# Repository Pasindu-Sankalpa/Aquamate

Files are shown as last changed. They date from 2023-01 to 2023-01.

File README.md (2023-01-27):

<b><h2><center>Problem Description</center></h1></b>

Although it is unpopular, fish breeding is an important source of foreign exchange for Sri Lanka. In the middle level it is self-employment for a vast population. Not only that, most of the people also have a home aquarium to refresh their minds. Accordingly, we can conclude that fish breeding has been spread to each level in society.

Temperature of water, pH level and turbidity are the main parameters which the fish breeders should keep on track regarding the safety of their farm. But as we observed, there is no such system deployed to measure these parameters in real time even in mass scale aquariums in Sri Lanka. Hence, this can lead to economic disasters if a parameter change happens. Another problem we can identify is the need of employees for feeding. Commonly, feeding is done once or twice per day. Therefore, if we can automate this process, it would be beneficial for the farm owners.

Our solution is Aquamate. A monitoring and automatic feeding system for mass scale aquariums in Sri Lanka.

Please refer the documents for more information

Visit <http://aquamate-global.web.app/>

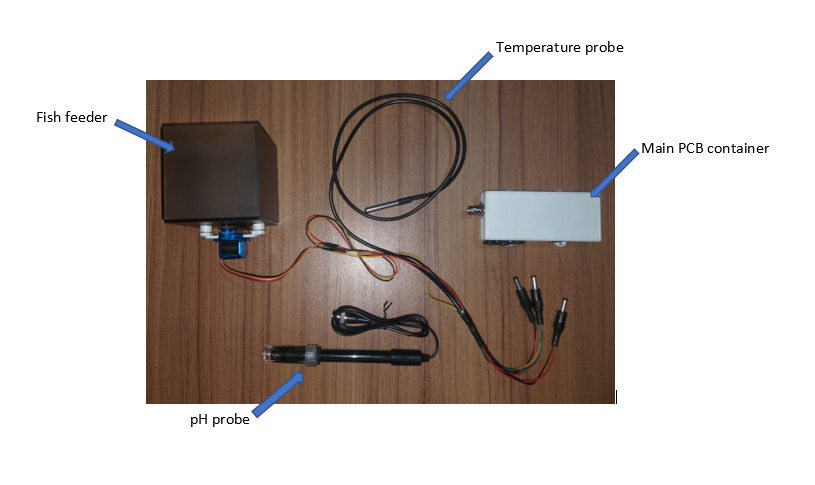
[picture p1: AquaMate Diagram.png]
AquaMate indoor unit

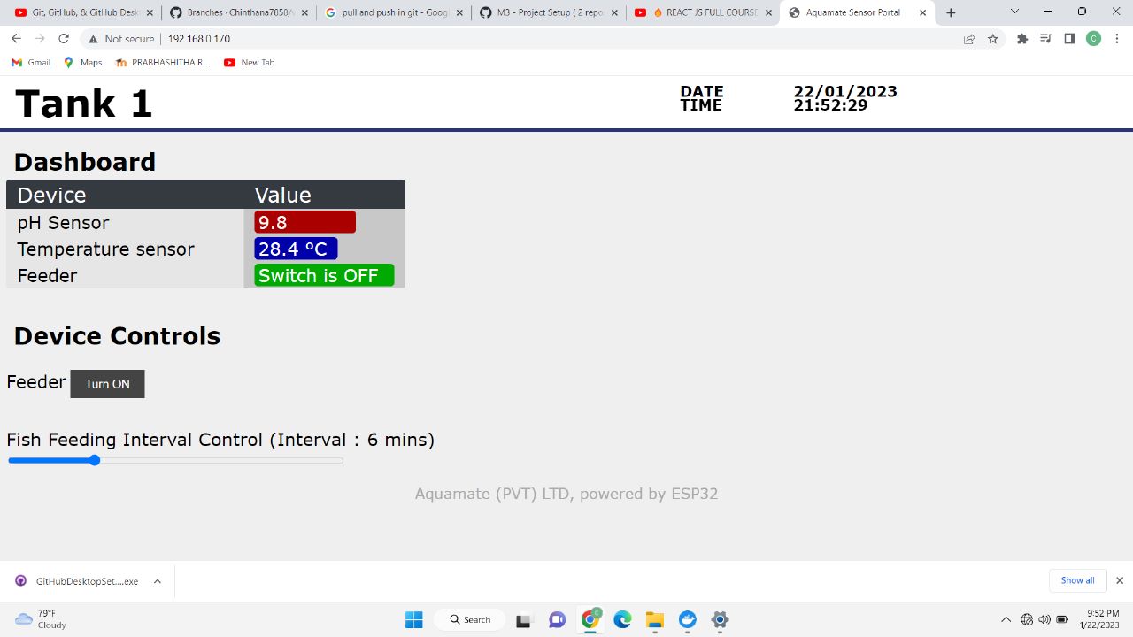
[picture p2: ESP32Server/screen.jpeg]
AquaMate server


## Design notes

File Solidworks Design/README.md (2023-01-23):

<b><h2><center>Enclosure Design</center></h1></b>

Enclosure design was designed with SOLIDWORKS 2020. There are two main parts such that fish feeder and main PCB container.

<br>
<br>

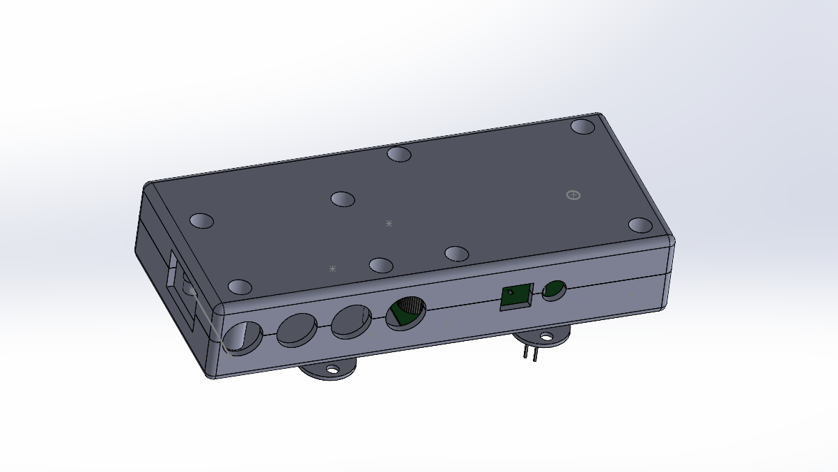
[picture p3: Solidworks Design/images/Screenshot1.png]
header image

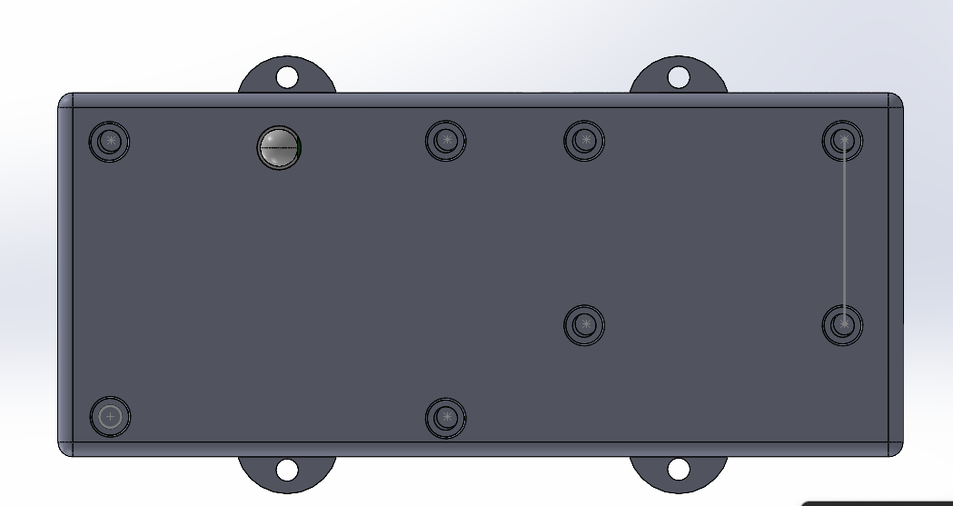
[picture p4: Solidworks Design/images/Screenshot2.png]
header image

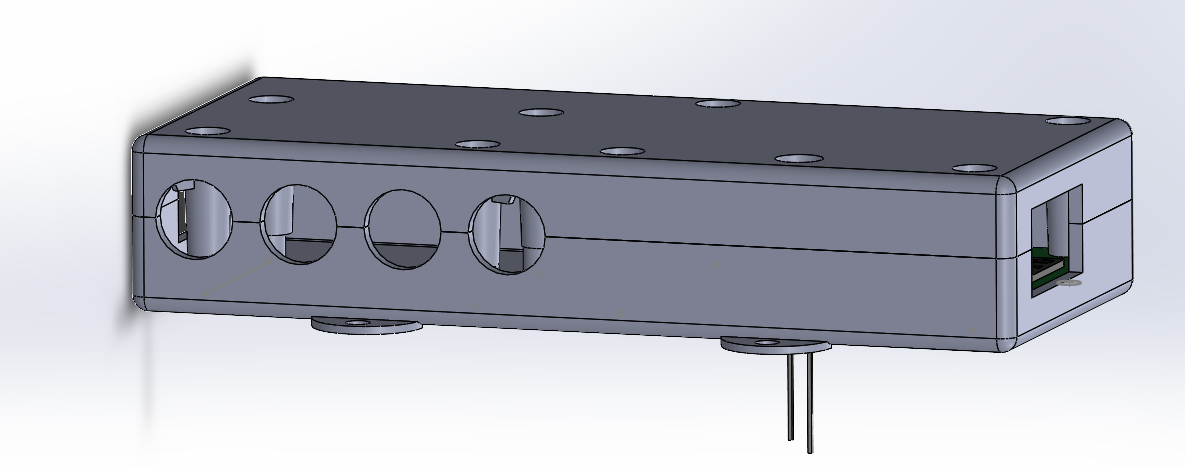
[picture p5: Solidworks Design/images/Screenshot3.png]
header image

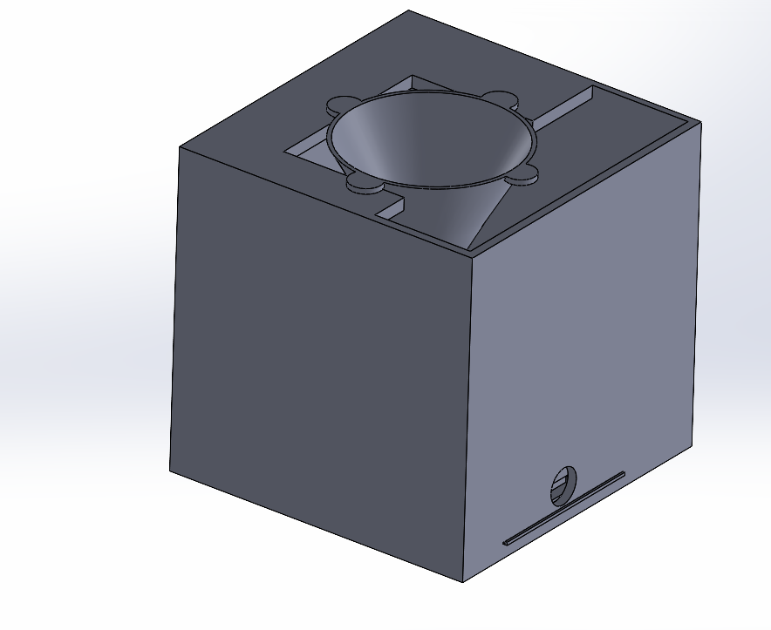
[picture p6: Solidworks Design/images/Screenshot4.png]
header image


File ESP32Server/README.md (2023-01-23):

<b><h2><center>Sampe code for updating a web page and getting user actions sent back the the microcontroller</center></h1></b>

This sample code will show you how to create an access point, serve a web page, updated just changed data, and get user interactions such as button presses and slider actions sent back to the microcontrller.

You will need an ESP32 and some open source libraries.

<br>
<br>

header image

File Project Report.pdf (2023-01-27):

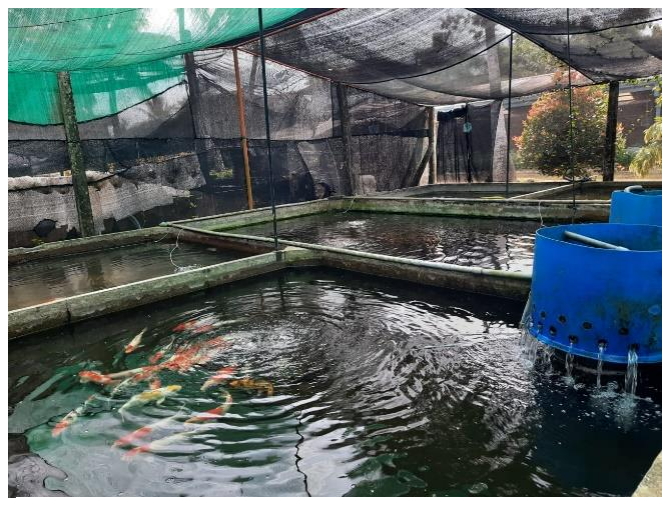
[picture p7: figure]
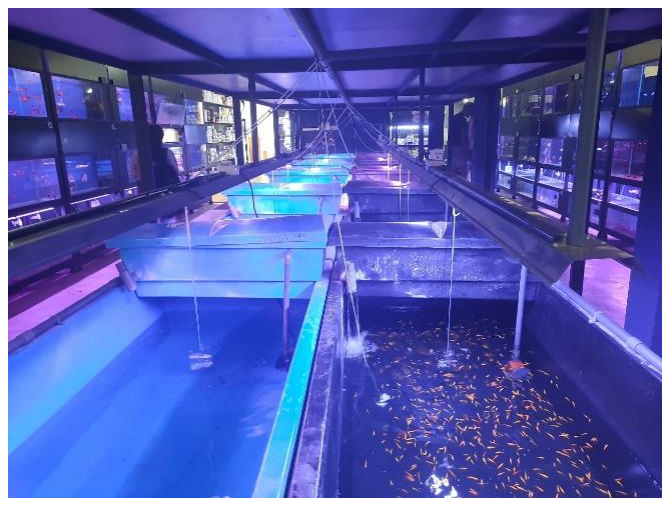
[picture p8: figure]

Figure: Indoor tank | Figure: Outdoor tank

## 1. Problem Description

Although it is unpopular, fish breeding is an important source of foreign exchange for Sri Lanka. In the middle level it is self-employment for a vast population. Not only that, most of the people also have a home aquarium to refresh their minds. Accordingly, we can conclude that fish breeding has been spread to each level in society.

Temperature of water, pH level and turbidity are the main parameters which the fish breeders should keep on track regarding the safety of their farm. But as we observed, there is no such system deployed to measure these parameters in real time even in mass scale aquariums in Sri Lanka. Hence, this can lead to economic disasters if a parameter change happens. Another problem we can identify is the need of employees for feeding. Commonly, feeding is done once or twice per day. Therefore, if we can automate this process, it would be beneficial for the farm owners.

Several aquarium monitoring systems are available in the global market. The problems we can identify, when we are going to deploy them in Sri Lanka are,
1. High cost (approximately $ 500 per unit for an industrial level equipment)
2. Requirement of periodic service (this is also problematic because no service center located in Sri Lanka)

## 2. Problem Validation

We visited Angel Aquarium (pvt) Ltd. which is one of mass scale aquarium in Sri Lanka to get a better understanding regarding the problem. As explained in the above section they are also hoping to deploy this kind of system but the initial cost to purchase them from the global market is not affordable for them. This was a huge motivation for our team.

By this discussion, we could gather important information regarding the precious water parameters for fishes and feeding patterns. Another important fact we observed is that the pH level is critical for indoor fish species while the turbidity is the important parameter for the outdoor species. pH level is not critical for outdoor species since they have been adopted for varies pH levels such as rainy water, but the high turbidity can damage their branchia. However, temperature is critical for both indoor and outdoor species.

## 3. Solution

Our solution is Aquamate. A monitoring and automation system for mass scale aquariums in Sri Lanka. Our mission is to provide this product in an affordable price.

Under the reasons explained earlier, we introduce two separate units for indoor and outdoor tanks. By this method we can reduce the cost for un-necessary sensors.

Under this project we implement only the indoor unit. Table 1 lists the features each unit has. The feeder is programmable via the dashboard to feed at any time interval.

Feature | Indoor Unit | Outdoor Unit
Temperature sensor | Yes | Yes
pH sensor | Yes | No
Turbidity sensor | No | Yes
Feeder | Yes | Yes
Dashboard | Yes | Yes

## 4. Implementation

### 4.1 Component Selection

Follows are how we selected the critical components of our device.

Micro controller: Selected micro controller is ESP32 wroom 32 (https://www.espressif.com/sites/default/files/documentation/esp32-wroom-32_datasheet_en.pdf) considering its WiFi capability and low power usage. ESP8266 is also a good alternative which comes under the same family with low price, however since we need two ADC lines we had to move to ESP32 wroom 32 with the an additional cost.

pH sensor: Gravity: Analog pH Sensor (https://www.dfrobot.com/product-2069.html) which comes with an industrial level probe is selected considering its considerable accuracy and relative low cost.

Temperature sensor: DS18B20 (https://www.analog.com/media/en/technical-documentation/data-sheets/ds18b20.pdf) is selected. It is water resist and has an excellent accuracy.

### 4.2 Circuit Design and Initial Testing

The device is planned to be powered by a 9V supply. There are two reasons behind this decision

1. If we use 230V AC current to power the device, there has to be a 230V AC current wiring around the aquarium. Since aquariums always deal with water, we decided to power the device with 9V considering the user safety in a case of current leakage.
2. Additionally, it reduces the cost per unit since multiple devices can be powered with a single power supply. No need of adding a transformer and relative circuitry for every device.

Table 1: Features of units

There are two voltage regulator ICs inside a device. AMS1117-3.3v regulator is used to power the micro controller and the temperature sensor. AMS1117-5v regulator is used to power the pH sensor and feeder.

Initial testing was carried out using a ESP32 development kit. A breadboard prototype was implemented to test the sensors. Temperature sensor was tested in our own and pH sensor was tested with the help of department of material science and engineering.

### 4.3 Printed Circuit Board Design

Printed circuit board was designed with Altium Designer 21.0.8. It was two-layer design. Two push buttons were added on the PCB for testing purposes and can be removed in a mass scale manufacturing.

Manufacturing was done at JLCPCB in China. Therefore, online available JLCPCB design rules were imported to Altium Designer.

Refer Appendix A and Appendix B for schematic diagram and layout respectively.

### 4.4 Enclosure Design

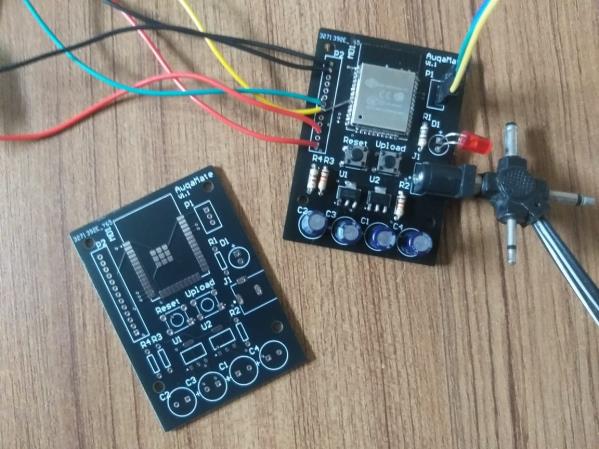
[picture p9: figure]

Enclosure design was designed with SOLIDWORKS 2020. There are two main parts such that fish feeder and main PCB container.

### 4.4.1 Fish feeder

This is a cube shaped box. There is a lid that opens and closes to fall fish seeds into the tank at the specified time interval. There are two mounting bosses in the bottom side to fix the servo motor that is used to open and close the lid.

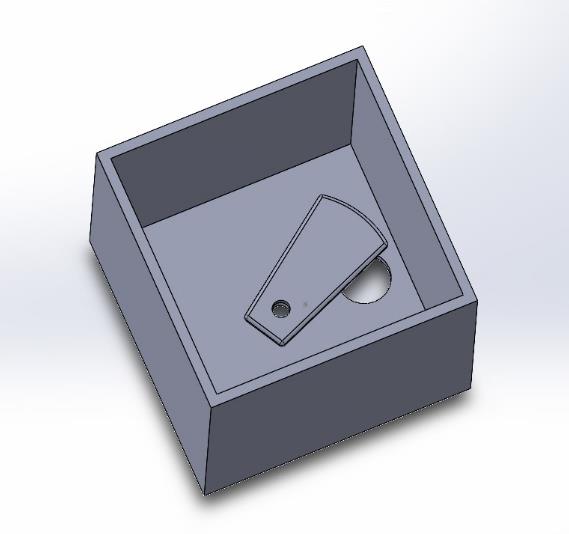
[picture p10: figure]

### 4.4.2 Main PCB Container

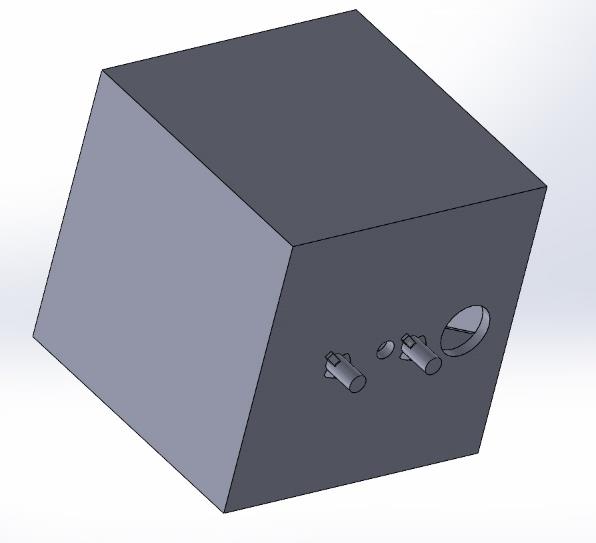
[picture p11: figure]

This was designed to contain the main PCB and pH sensor unit. Two circuit parts are fixed to the box using four mounting bosses. There are four holes to fix sensors.

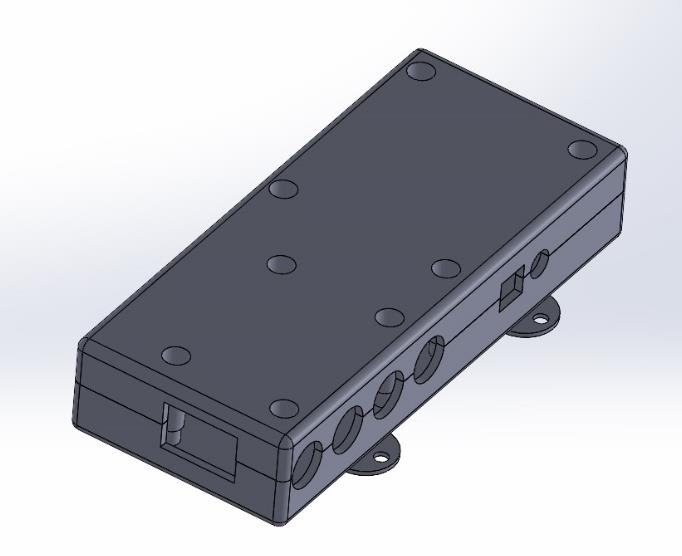
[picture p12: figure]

### 4.5 Web Development

### 4.5.1 Web Page

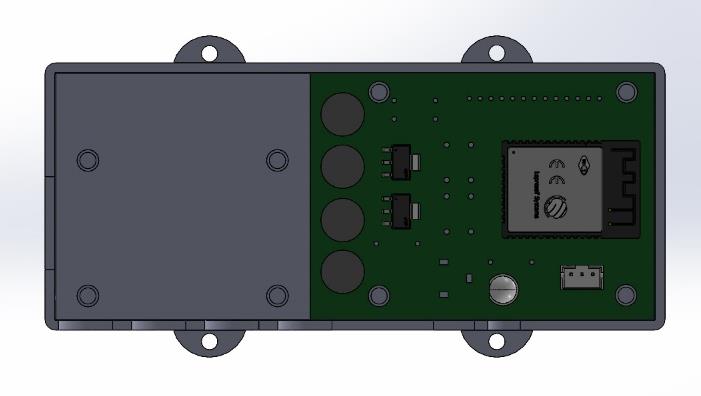
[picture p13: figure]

Main web site can be accessed by anyone using the link http://aquamate-global.web.app. An image of interface is shown below.

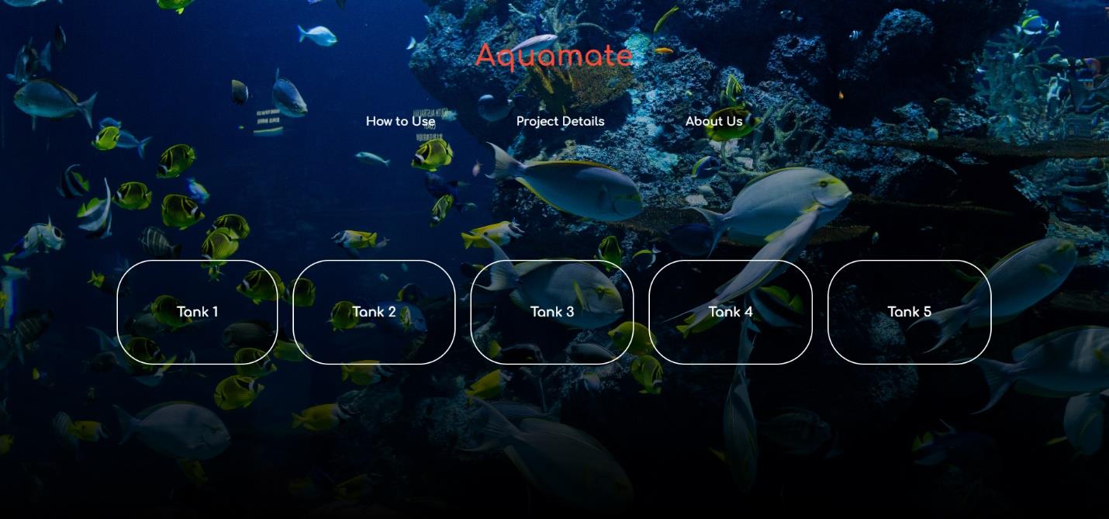
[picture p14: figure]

Users can click relevant button with tank name to see the corresponding dashboard. It will pop-up in a new window. But those details can only be accessed by the people who have connected to the same local network, as same network which the Aquamate device is connected.

If the user is powering up the Aquamate device for the very first time, there is a small configuration needs to be done. Those details are shown in the web page as well.

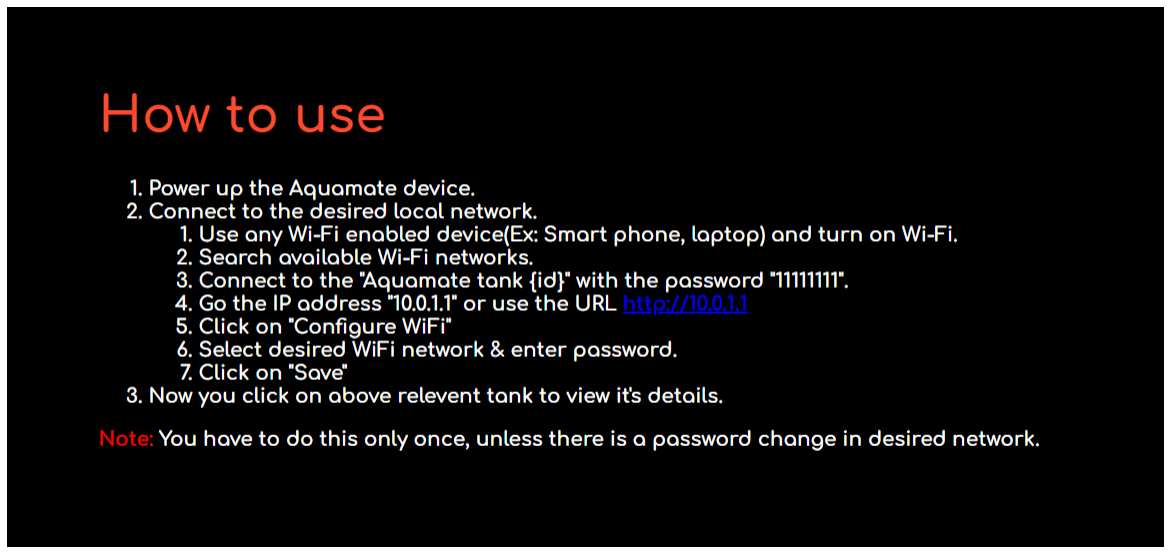
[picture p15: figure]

Above steps can be carried out by anyone who has basic knowledge of computer networks. Most importantly, these steps need to be done only once for each device. After that when powering on, Aquamate device will automatically connect to the previously configured local network.

### 4.5.2 ESP32 Web Server

Each Aquamate device has a web server running inside the ESP32 micro controller. After connected to the local network, it will send real time data of pH value, temperature, feeder on/off status to the web site continuously. So, the users can view the data.

pH progress bar shows pH values from 0 to 14 as standard scale. And temperature progress bar shows temperature values from 0ºC to 50ºC. If pH value or temperature value is too low or too high, color of the progress bar will change from blue to red. An instance of dashboard of a tank is shown below.

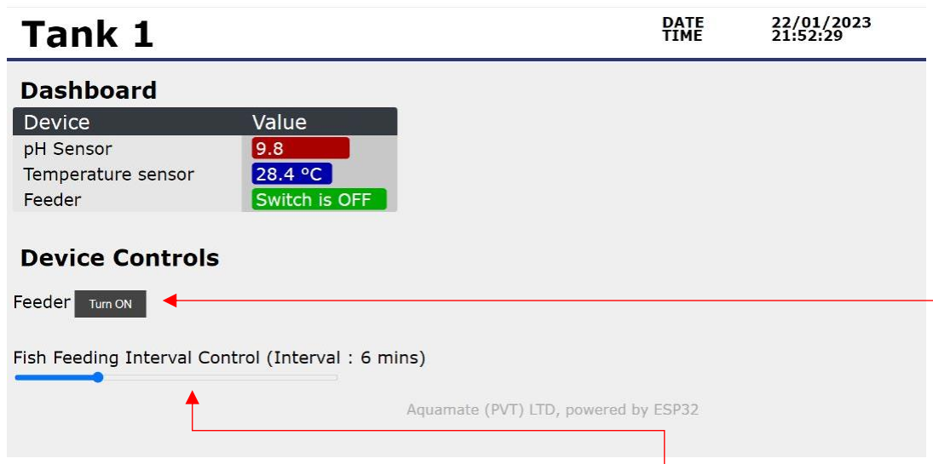
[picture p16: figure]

As well as users can set the fish feeding time interval using the slider in web page and feeder on/off switch. Slider can change the fish feeding interval between 1 to 24 hours. Those data will send back to the ESP32 web server and will act accordingly.

### 4.6 Final Testing

After completing and assembling all components a final testing was carried out to check the overall functionality. Things works perfectly and communicate with the web server without any failure. Figure below shows the parts of Aquamate indoor unit.

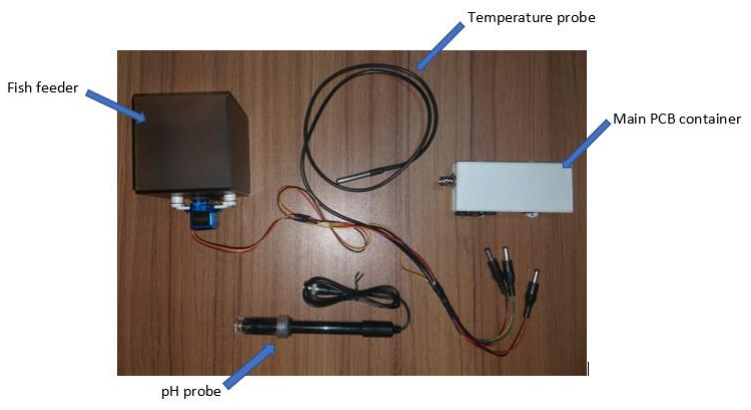
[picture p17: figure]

## Appendix A

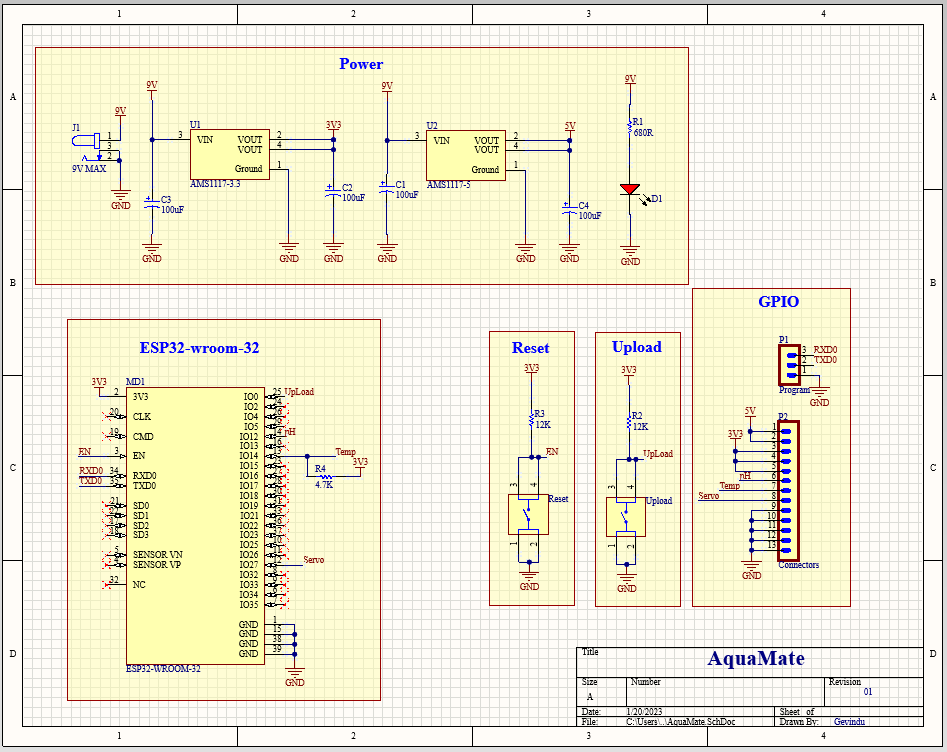
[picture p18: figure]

## Appendix B

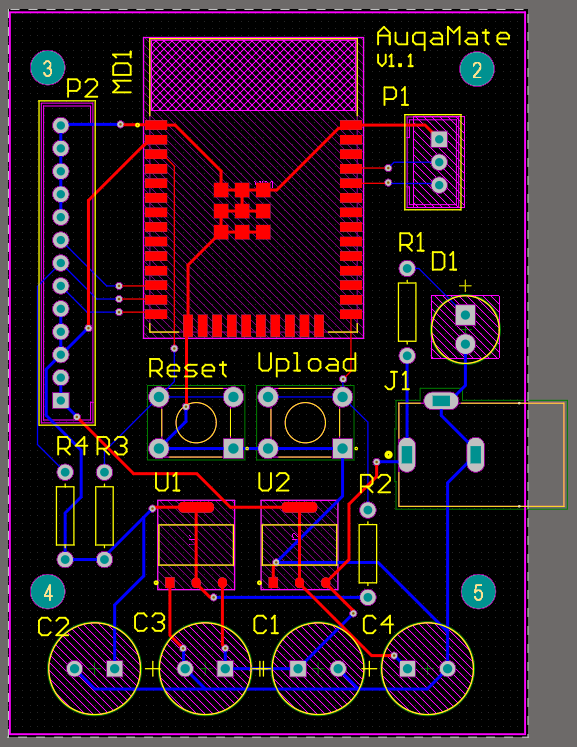
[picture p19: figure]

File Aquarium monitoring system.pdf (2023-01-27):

# Aquamate

Aquamate is an aquarium monitoring and automation system for mass scale aquariums in Sri Lanka. we introduce two separate units for indoor and outdoor tanks. By this method we can reduce the cost for un-necessary sensors. We implement only the indoor unit. We used temperature sensor and pH sensor for this unit. We can measure pH value and temperature of indoor tank. There is a dashboard for this unit. Parallelly, we designed a fish feeder. The fish feeder is programmable via the dashboard to feed at any time interval.

Mainly there are two main parts of this unit. They are fish feeder and PCB contained box. pH sensor unit and main PCB is contained in this box. All sensors are connected to this box. Fish feeder is a cube shaped box. There is a lid that opens and closes to fall fish seeds into the tank at the specified time interval.

This is a user-friendly monitoring system. We have a web page and user can watch necessary information of the fish tank through that webpage. And also, user can control the fish feeder unit through this webpage. You can connect several tanks to monitoring system. Each tank has separate tab in our webpage. Our sensors are smoothly calibrated and you will have more accurate values. Our main unit is waterproof and well designed.

Main web site can be accessed by anyone using the link http://aquamate-global.web.app. Users can click relevant button with tank name to see the corresponding dashboard. It will pop-up in a new window. But those details can only be accessed by the people who have connected to the same local network, as same network which the Aquamate device is connected. If the user is powering up the Aquamate device for the very first time, there is a small configuration needs to be done. Those details are shown in the web page as well. Those steps can be carried out by anyone who has basic knowledge of computer networks. Most importantly, these steps need to be done only once for each device. After that when powering on, Aquamate device will automatically connect to the previously configured local network.

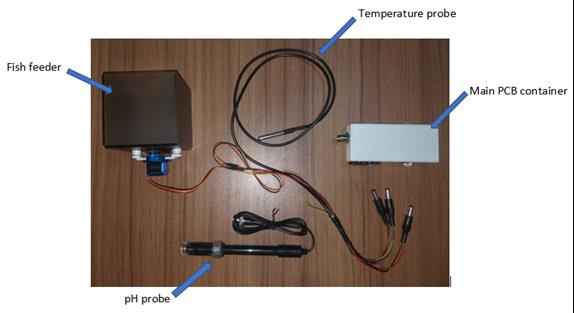
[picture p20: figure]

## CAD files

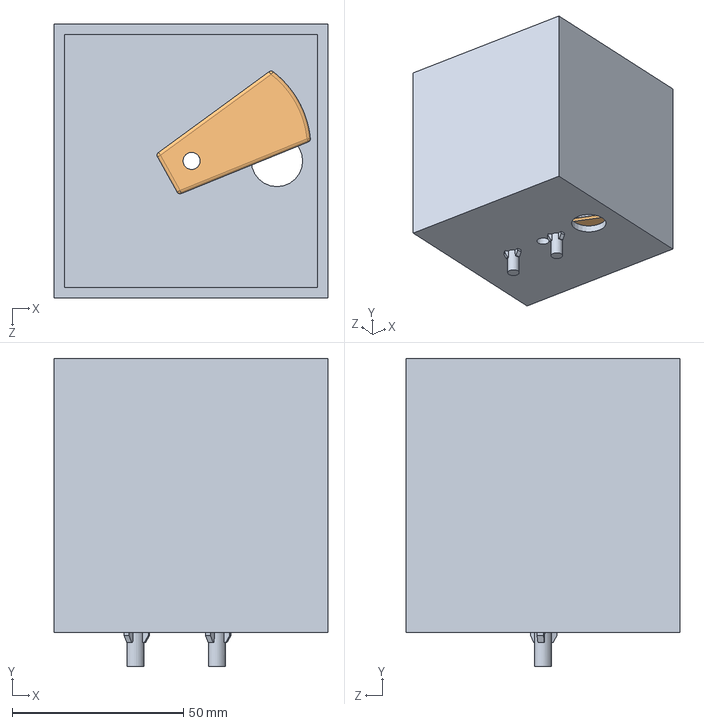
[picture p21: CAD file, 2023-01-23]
Solidworks Design/Fish_feeder.SLDASM
80.0 x 90.0 x 80.0 mm
Part1^Assem2
Part2^Assem2

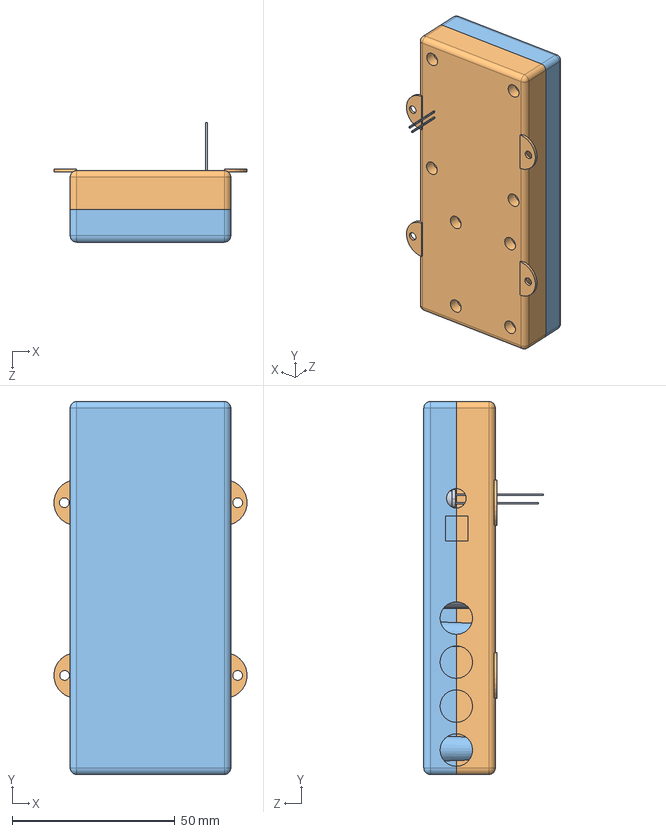
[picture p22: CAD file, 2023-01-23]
Solidworks Design/Main_pcb.SLDASM
59.2 x 114.5 x 36.7 mm
AquaMate.step
Part2^Assem1
Part3^Assem1

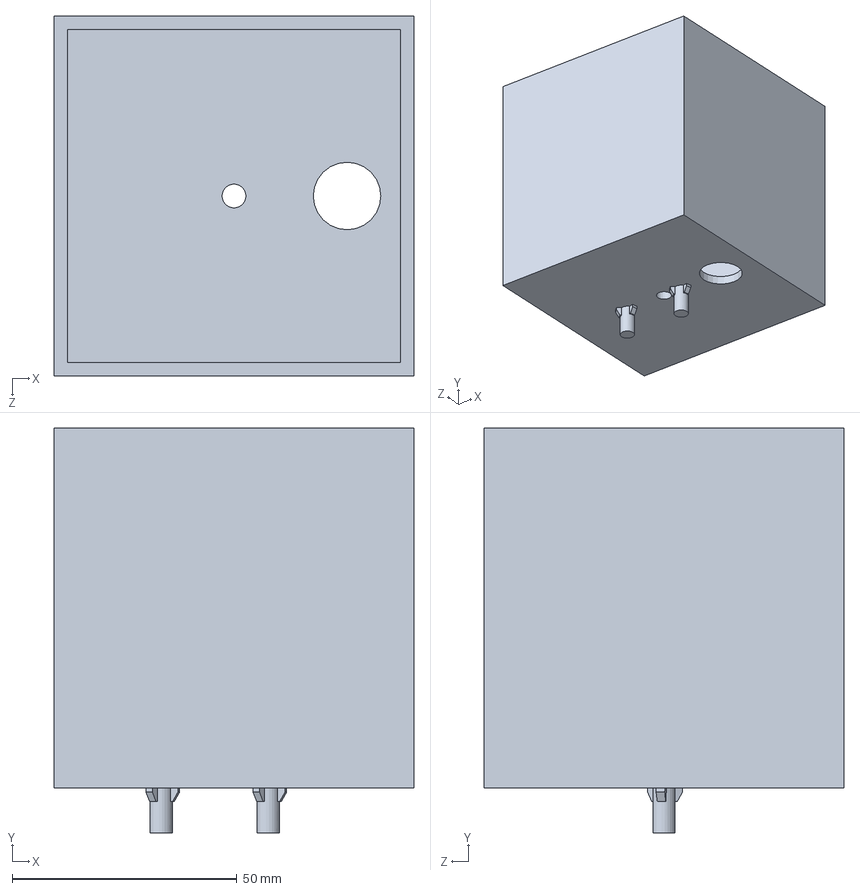
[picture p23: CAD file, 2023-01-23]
Solidworks Design/Part1^Assem2.SLDPRT
80.0 x 90.0 x 80.0 mm

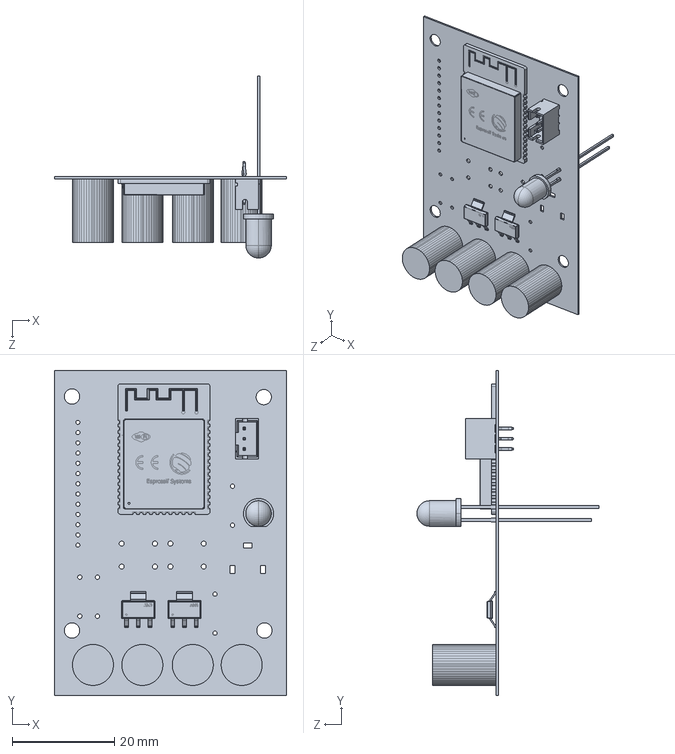
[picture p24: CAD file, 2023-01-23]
Solidworks Design/AquaMate.step.SLDPRT
45.3 x 63.5 x 35.6 mm

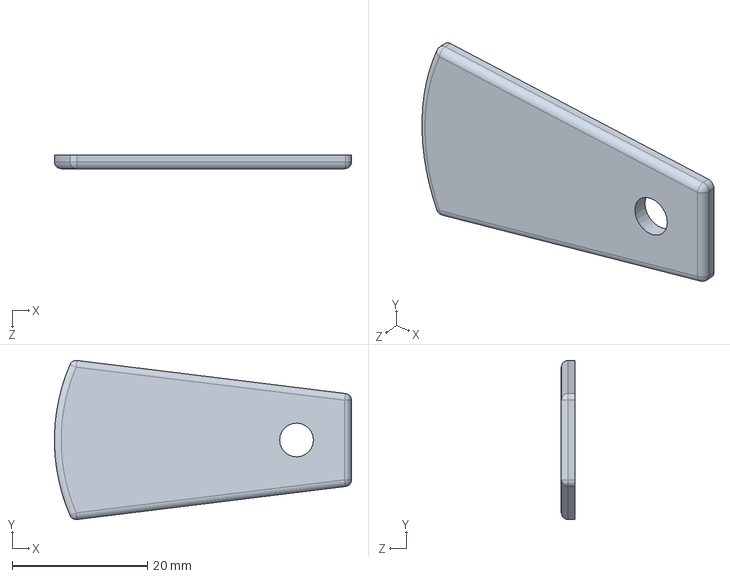
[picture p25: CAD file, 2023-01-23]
Solidworks Design/Part2^Assem2.SLDPRT
43.9 x 23.5 x 2.00 mm

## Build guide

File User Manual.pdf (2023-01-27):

# Aquamate (PVT) LTD

# Aquarium Monitoring System

# User Manual

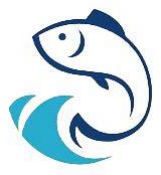
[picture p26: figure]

## *Before operating the appliance, please read this manual and all the safety instructions thoroughly

and retain it for future reference.

## FOR PERFECT RESULTS

Thank you for choosing Aquamate Monitoring System for your aquarium. Aquamate featuring advance design, cutting-edge technology, high reliability and quality construction. Please read this manual carefully and keep it for future reference.
Visit our website for:

Get usage advice, brochures, trouble shooter, service information: https://aquamate-global.web.app/

## INTRODUCTION

Aquamate is the user-friendly monitoring system. We have a web page and user can watch necessary information of the fish tank through that webpage. And also, user can control the fish feeder unit through this webpage. You can connect several tanks to monitoring system. Each tank has separate tab in our webpage. Our sensors are smoothly calibrated and you will have more accurate values. Our main unit is waterproof and well designed.

This User Manual (UM) provides the information necessary for aquarists (who work in aquariums) to effectively use the Aquamate monitoring system.

## SAFETY INFORMATION

Before the installation and use of the appliance, carefully read the supplied instructions. The manufacturer is not responsible for any injuries or damages that are the result of incorrect installation. Always keep the instructions in a safe and accessible location for future reference.

1. Must use 230V AC 50Hz. The electrical outlet should connect with earth line.
2. Temperature sensor range in -50°C to 125°C.
3. Ph sensor put on the water temperature should within 0-80°C.
4. Main unit should not put inside a water.

## INSTALLATION

1. Main unit should place near the tank (should not put inside water.)
2. Temperature sensor and PH sensor completely put inside a water.
3. feeder unit should place on the water tank.

## MAINTENANCE & TROUBLE SHOOTING

1. PH sensor probe need to replace after 1-2 years.
2. Please clean the main unit when its dirty.
3. if device malfunctioning or not working please contact us.

## SET-UP CONSIDERATIONS

1. Power up the Aquamate device.
2. Connect to the desired local network.
1. Use any Wi-Fi enabled device (Ex: Smart phone, laptop) and turn on Wi-Fi.
2. Search available Wi-Fi networks.
3. Connect to the “Aquamate tank {id}” with the password “11111111”.
4. Go the IP address “10.0.1.1” or use the URL http://10.0.1.1.
5. Click on “Configure WiFi”.
6. Select desired WiFi network & enter password.
7. Click on “Save”.
3. Now you click on above relevant tank to view its details.

## PRODUCT DESCRIPTION

1. BNC connector of pH sensor unit
2. Servo power
3. Servo signal
4. Temperature power
5. Temperature signal
6. Power supply
7. LED bulb

1
2

6

7
3 | 4 | 5

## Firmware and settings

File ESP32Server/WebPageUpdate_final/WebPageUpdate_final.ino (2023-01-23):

/*
  this example will show
  1. how to use and ESP 32 for reading pins
  2. building a web page for a client (web browser, smartphone, smartTV) to connect to
  3. sending data from the ESP to the client to update JUST changed data
  4. sending data from the web page (like a slider or button press) to the ESP to tell the ESP to do something

  If you are not familiar with HTML, CSS page styling, and javascript, be patient, these code platforms are
  not intuitive and syntax is very inconsitent between platforms

  I know of 4 ways to update a web page
  1. send the whole page--very slow updates, causes ugly page redraws and is what you see in most examples
  2. send XML data to the web page that will update just the changed data--fast updates but older method
  3. JSON strings which are similar to XML but newer method
  4. web sockets very very fast updates, but not sure all the library support is available for ESP's

  I use XML here...

  compile options
  1. esp32 dev module
  2. upload speed 921600
  3. cpu speed 240 mhz
  flash speed 80 mhz
  flash mode qio
  flash size 4mb
  partition scheme default

  NOTE: if your ESP fails to program press the BOOT button during programm when the IDE is "looking for the ESP"
  NOTE: there are 6 changes to make to switch from ESP32 to ESP8266 or vise versa.
*/
#include <WiFiManager.h>       // library for Option 3
#include "WebData.h"           // .h file that stores your html page code

// >>>>>>>>>>>>>>>>>>>>>>>>>>>>>>>>>>>>>>>>>>>>>>>>>>>>[1] For ESP8266
// #include <ESP8266WiFi.h>       // standard library
// #include <ESP8266WebServer.h>  // standard library
// >>>>>>>>>>>>>>>>>>>>>>>>>>>>>>>>>>>>>>>>>>>>>>>>>>>>[1] For ESP32
#include <WiFi.h>       // standard library
// Note: For ESP32,
// ADC1 controls ADC function for pins GPIO 32-39
// ADC2 controls ADC function for pins GPIO 0, 2, 4, 12-15, 25-27
// ADC2 pins cannot work when WiFi is in use.
#include <WebServer.h>  // standard library

// Libraries for temperature sensor
#include <OneWire.h>
#include <DallasTemperature.h>

// Libraries for servo
#include <ESP32_Servo.h>

// here you post web pages to your home's intranet which will make page debugging easier, as you just need to refresh the browser as opposed to reconnection to the web server.
// uncomment one line on your preference.
// #define USE_INTRANET
// #define USE_AP
#define USE_WiFi

// replace this with your homes intranet connect parameters (for Option 1)
#define LOCAL_SSID "Dialog 4G"
#define LOCAL_PASS "DABDFFF8DE4"

// once you are ready to go live, these settings are what you client will connect to (for Option 2 and Option 3)
#define AP_SSID "Aquamate Tank 1"
#define AP_PASS "11111111"

// defines for pins for sensors, outputs etc.
#define PIN_OUT_0 16  // Output 1 (On board LED is D4 or GPIO2)
#define PIN_OUT_1 18  // Output 2
#define PIN_PWM 27    // PWM signal to control a fan speed
#define PIN_A0 33     // analog input of pH sensor
#define PIN_A1 14     // anaog input of temperature sensor

// variables to store measure data and sensor states
bool Device0 = false, Device1 = false;

int PWMRange = 0;

// >>>>>>>>>>>>>>>>>>>>>>>>>>>>>>>>>>>>>>>>>>>>>>>>>>>>[2] Setting of PWM properties (Only for ESP32)
const int pwm_ch = 0;
const int pwm_freq = 1000;
const int pwm_res = 8;

int BitsA0 = 0;
float VoltsA0 = 0;
float BitsA1 = 0, VoltsA1 = 0; // temperature in Celsius

uint32_t SensorUpdate = 0;
uint32_t FeederUpdate = 0;
uint32_t FeederDelay = 0;
bool servo_state = false;

// the XML array size needs to be bigger that your maximum expected size. 2048 is way too big for this example
char XML[2048];

// just some buffer holder for char operations
char buf[32];

// pH sensor parameters
int avg_phValue;   //Store the average value of the sensor feedback
int ph_buf[10],temp;

// temperature sensor parameters
OneWire oneWire(PIN_A1);                // setup a oneWire instance
DallasTemperature tempSensor(&oneWire); // pass oneWire to DallasTemperature library

Servo servo_1;

// variable for the IP address
IPAddress ip;

// static wifi configuration, instead of DHCP
IPAddress s_PageIP(192, 168, 0, 170);
IPAddress s_gateway(192, 168, 0, 1);
IPAddress s_subnet(255, 255, 255, 0);

// custom AP configuration
IPAddress PageIP(10,0,1,1);
IPAddress gateway(10,0,1,1);
IPAddress subnet(255,255,255,0);

// declare an object of ESP8266WebServer library
// >>>>>>>>>>>>>>>>>>>>>>>>>>>>>>>>>>>>>>>>>>>>>>>>>>>>[3] For ESP8266
// ESP8266WebServer server(80);
// >>>>>>>>>>>>>>>>>>>>>>>>>>>>>>>>>>>>>>>>>>>>>>>>>>>>[3] For ESP32
WebServer server(80);

void setup() {

  // standard stuff here
  // >>>>>>>>>>>>>>>>>>>>>>>>>>>>>>>>>>>>>>>>>>>>>>>>>>>>[4] For ESP8266
  //Serial.begin(115200);
  // >>>>>>>>>>>>>>>>>>>>>>>>>>>>>>>>>>>>>>>>>>>>>>>>>>>>[4] For ESP32
  Serial.begin(9600);
  tempSensor.begin();    // initialize the sensor

  servo_1.attach(PIN_PWM);
  servo_1.write(90);
  pinMode(PIN_OUT_0, OUTPUT);
  pinMode(PIN_OUT_1, OUTPUT);

  // turn off devices by default
  digitalWrite(PIN_OUT_0, Device0);
  digitalWrite(PIN_OUT_1, Device1);

  // configure PWM functionalitites
  // >>>>>>>>>>>>>>>>>>>>>>>>>>>>>>>>>>>>>>>>>>>>>>>>>>>>[5] For ESP8266
  // analogWrite(PIN_PWM, PWMRange);
  // >>>>>>>>>>>>>>>>>>>>>>>>>>>>>>>>>>>>>>>>>>>>>>>>>>>>[5] For ESP32
  // ledcSetup(pwm_ch, pwm_freq, pwm_res);
  // ledcAttachPin(PIN_PWM, pwm_ch); //there are 16 pwm channels from 0 to 15
  // ledcWrite(pwm_ch, PWMRange);
  
  delay(1000);

  // just an update to progress
  Serial.print("Starting server \n");
  Serial.print("--------------- \n");

  // Option 1
  // if you have this #define USE_INTRANET, you will connect to your home intranet, again makes debugging easier.
  // for this you can only connect to above defined home intranet
  #ifdef USE_INTRANET
    //static ip configuration
    if (!WiFi.config(s_PageIP, s_gateway, s_subnet)) {
      Serial.print("WiFi Configuration failed. \n");
    }
    WiFi.begin(LOCAL_SSID, LOCAL_PASS);
    // check ESP is connected to a wi-fi network
    while (WiFi.status() != WL_CONNECTED) {
      delay(500);
      Serial.print(".");
    }
    Serial.print("\n");
    Serial.print("WiFi connected..! \n");
    printWifiStatus();
  #endif

  // Option 2
  // if you have this #define USE_AP, ESP will create a soft access point.
  // (an intranet with no internet connection. But Clients can connect to your intranet and see the web page you are about to serve up.)
  #ifdef USE_AP
    //set custom ip for portal
    WiFi.softAPConfig(PageIP, gateway, subnet);
    delay(100);
    WiFi.softAP(AP_SSID, AP_PASS);
    delay(100);
    ip = WiFi.softAPIP();
    Serial.print("Access Point Created..! \n");
    Serial.print("SSID: "); Serial.println(AP_SSID);
    Serial.print("IP address: "); Serial.println(ip);
  #endif

  // Option 3
  // if you have this #define USE_WiFi, ESP will use WiFi manager.
  // Connect to an available any WiFi network (should know the password)
  #ifdef USE_WiFi
    WiFi.mode(WIFI_STA);
    WiFiManager wm;
    // If we don't reset WiFi manager settings, ESP will automatically connect to the previously connected network, if it's password is unchanged.
    //>>>>>>>>>>>>>>>>>>>>>>>>>>>>>>>>>>>>>>>>>>>>>>>>>>>>>>>>>>>>>>>>>>>>>>>>>>>>>>>>>>>>
    //wm.resetSettings(); //reset previous ssids
    //set custom ip for portal
    wm.setAPStaticIPConfig(PageIP, gateway, subnet);
    //static ip configuration
    //>>>>>>>>>>>>>>>>>>>>>>>>>>>>>>>>>>>>>>>>>>>>>>>>>>>>>>>>>>>>>>>>>>>>>>>>>>>>>>>>>>>>
    //wm.setSTAStaticIPConfig(s_PageIP, s_gateway, s_subnet);
    bool res;
    res  = wm.autoConnect(AP_SSID, AP_PASS);
    Serial.println();
    if (!res) {
      Serial.println("WiFi connecting failed.");
      ESP.restart();
    }
    else {
      Serial.println("WiFi connected..!");
    }
    printWifiStatus();
  #endif

  Serial.print("\n\n");

  // these calls will handle data coming back from your web page
  // this one is a page request, upon ESP getting / string the web page will be sent
  server.on("/", SendWebsite);

  // upon esp getting /XML string, ESP will build and send the XML, this is how we refresh just parts of the web page
  server.on("/xml", SendXML);

  // upon ESP getting /UPDATE_SLIDER string, ESP will execute the UpdateSlider function
  // same notion for the following .on calls
  // add as many as you need to process incoming strings from your web page
  // as you can imagine you will need to code some javascript in your web page to send such strings
  // this process will be documented in the SuperMon.h web page code
  server.on("/UPDATE_SLIDER", UpdateSlider);
  server.on("/BUTTON_0", ProcessButton_0);
  server.on("/BUTTON_1", ProcessButton_1);

  // finally begin the server
  server.begin();
}

void loop() {
  // you main loop that measures, processes, runs code, etc.
  // note that handling the "on" strings from the web page are NOT in the loop
  // that processing is in individual functions all managed by the wifi lib

  // in my example here every 50 ms, i measure some analog sensor data (my finger dragging over the pins and process accordingly.
  // analog input can be temperature sensors, light sensors, digital pin sensors, etc.
  if ((millis() - SensorUpdate) >= 50) {
    //Serial.println("Reading Sensors");
    SensorUpdate = millis();
    
    //BitsA0 = analogRead(PIN_A0);
    //BitsA1 = analogRead(PIN_A1);

    phSense();
    
    tempSensor.requestTemperatures();             // send the command to get temperatures
    BitsA1 = tempSensor.getTempCByIndex(0)+ 1.2;  // read temperature in Celsius
    VoltsA1 = BitsA1;
  }

  if ((Device0 == 1) && ((millis() - FeederUpdate) >= 3600000*PWMRange)) {
    //Serial.print("servo on ");
    servo_1.write(0);
    FeederUpdate = millis();
    FeederDelay = FeederUpdate;
    servo_state = true;
  }
  if ((servo_state == true) && ((millis() - FeederDelay) >= 10000)) {
    //Serial.print("servo off ");
    servo_1.write(90);
    servo_state = false;
  }
  
  // no matter what, you must call this handleClient repeatidly--otherwise the web page will not get instructions to do something.
  server.handleClient();
}

void phSense() {
  for(int i=0;i<10;i++)       //Get 10 sample value from the sensor for smooth the value
  {
    ph_buf[i]=analogRead(PIN_A0);
  }
  for(int i=0;i<9;i++)        //sort the analog from small to large
  {
    for(int j=i+1;j<10;j++)
    {
      if(ph_buf[i]>ph_buf[j])
      {
        temp=ph_buf[i];
        ph_buf[i]=ph_buf[j];
        ph_buf[j]=temp;
      }
    }
  }
  avg_phValue=0;
  for(int i=2;i<8;i++)             //take the average value of 6 center sample
    avg_phValue+=ph_buf[i];
  BitsA0=avg_phValue/6;
  VoltsA0=BitsA0*3.3*3.3/4095-1;     //convert the analog into ph value
}

// function managed by an .on method to handle slider actions on the web page
// this example will get the passed string called VALUE and convert to a pwm value and control the fan speed
void UpdateSlider() {

  // many I hate strings, but wifi lib uses them...
  String t_state = server.arg("VALUE");

  // convert the string sent from the web page to an int
  PWMRange = t_state.toInt();
  // Serial.print("UpdateSlider"); Serial.println(PWMRange);
  // now set the PWM duty cycle
  // >>>>>>>>>>>>>>>>>>>>>>>>>>>>>>>>>>>>>>>>>>>>>>>>>>>>[6] For ESP8266
  // analogWrite(PIN_PWM, PWMRange);
  // >>>>>>>>>>>>>>>>>>>>>>>>>>>>>>>>>>>>>>>>>>>>>>>>>>>>[6] For ESP32
  // ledcWrite(pwm_ch, PWMRange);

  // YOU MUST SEND SOMETHING BACK TO THE WEB PAGE--BASICALLY TO KEEP IT LIVE

  // option 1: send no information back, but at least keep the page live
  // just send nothing back
  // server.send(200, "text/plain", ""); //Send web page

  // option 2: send something back immediately, maybe a pass/fail indication, maybe a measured value.
  // here is how you send data back immediately and NOT through the general XML page update code.
  // my simple example guesses at fan speed--ideally measure it and send back real data.
  // i avoid strings at all caost, hence all the code to start with "" in the buffer and build a simple piece of data.
  strcpy(buf, "");
  sprintf(buf, "%d", PWMRange);
  sprintf(buf, buf);

  // now send it back
  server.send(200, "text/plain", buf); //Send web page
}

// now process button_0 press from the web site. Typical applications are the used on the web client can turn on/off a light, a fan, disable something etc.
void ProcessButton_0() {

  Device0 = !Device0;
  digitalWrite(PIN_OUT_0, Device0);
  Serial.print("Button 0 "); Serial.println(Device0);
  // regardless if you want to send stuff back to client or not you must have the send line--as it keeps the page running,
  // if you don't want feedback from the MCU--or let the XML manage sending feeback.

  // option 1 -- keep page live but dont send any thing
  // here i don't need to send and immediate status, any status like the illumination status will be send in the main XML page update code
  server.send(200, "text/plain", ""); //Send web page

  // option 2 -- keep page live AND send a status
  // if you want to send feedback immediataly
  // note you must have reading code in the java script
  /*
    if (Device0) {
      server.send(200, "text/plain", "1"); //Send web page
    }
    else {
      server.send(200, "text/plain", "0"); //Send web page
    }
  */
}

// same notion for processing button_1
void ProcessButton_1() {

  // just a simple way to toggle a LED on/off. Much better ways to do this
  Serial.println("Button 1 press");
  Device1 = !Device1;

  digitalWrite(PIN_OUT_1, Device1);
  Serial.print("Button 1 "); Serial.println(Device1);
  // regardless if you want to send stuff back to client or not you must have the send line--as it keeps the page running
  // if you don't want feedback from the MCU--or send all data via XML use this method
  // sending feeback
  server.send(200, "text/plain", ""); //Send web page

  // if you want to send feedback immediataly
  // note you must have proper code in the java script to read this data stream
  /*
    if (Device1) {
      server.send(200, "text/plain", "SUCCESS"); //Send web page
    }
    else {
      server.send(200, "text/plain", "FAIL"); //Send web page
    }
  */
}

// code to send the main web page
// PAGE_MAIN is a large char defined in SuperMon.h
void SendWebsite() {
  Serial.println("sending web page");
  // you may have to play with this value, big pages need more porcessing time, and hence a longer timeout that 200 ms
  server.send(200, "text/html", PAGE_MAIN);
}

// code to send the main web page
// I avoid string data types at all cost, hence all the char manipulation code
void SendXML() {
  // Serial.println("sending xml");

  strcpy(XML, "<?xml version = '1.0'?>\n<Data>\n");

  // send bitsA0
  sprintf(buf, "<B0>%d.%d</B0>\n", (int) (BitsA0), abs((int) (BitsA0 * 10)  - ((int) (BitsA0) * 10)));
  strcat(XML, buf);
  // send Volts0
  sprintf(buf, "<V0>%d.%d</V0>\n", (int) (VoltsA0), abs((int) (VoltsA0 * 10)  - ((int) (VoltsA0) * 10)));
  strcat(XML, buf);

  // send bits1
  //sprintf(buf, "<B1>%d</B1>\n", BitsA1);
  sprintf(buf, "<B1>%d.%d</B1>\n", (int) (BitsA1), abs((int) (BitsA1 * 10)  - ((int) (BitsA1) * 10)));
  strcat(XML, buf);
  // send Volts1
  sprintf(buf, "<V1>%d.%d</V1>\n", (int) (VoltsA1), abs((int) (VoltsA1 * 10)  - ((int) (VoltsA1) * 10)));
  strcat(XML, buf);

  // show devices status
  if (Device0) {
    strcat(XML, "<DEVICE0>1</DEVICE0>\n");
  }
  else {
    strcat(XML, "<DEVICE0>0</DEVICE0>\n");
  }

  if (Device1) {
    strcat(XML, "<DEVICE1>1</DEVICE1>\n");
  }
  else {
    strcat(XML, "<DEVICE1>0</DEVICE1>\n");
  }

  strcat(XML, "</Data>\n");
  // wanna see what the XML code looks like?
  // actually print it to the serial monitor and use some text editor to get the size
  // then pad and adjust char XML[2048]; above
  Serial.println(XML);

  // you may have to play with this value, big pages need more porcessing time, and hence
  // a longer timeout that 200 ms
  server.send(200, "text/xml", XML);
}

// I think I got this code from the wifi example
void printWifiStatus() {
  // print the SSID of the network you're attached to:
  Serial.print("SSID: ");
  Serial.println(WiFi.SSID());

  // print your WiFi shield's IP address:
  ip = WiFi.localIP();
  Serial.print("IP Address: ");
  Serial.println(ip);

  // print the received signal strength:
  long rssi = WiFi.RSSI();
  Serial.print("signal strength (RSSI):");
  Serial.print(rssi);
  Serial.println(" dBm");
  // print where to go in a browser:
  Serial.print("Open http://");
  Serial.println(ip);
}

// end of code

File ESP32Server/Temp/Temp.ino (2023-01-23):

/*
 * Created by ArduinoGetStarted.com
 *
 * This example code is in the public domain
 *
 * Tutorial page: https://arduinogetstarted.com/tutorials/arduino-temperature-sensor
 */

#include <OneWire.h>
#include <DallasTemperature.h>

const int PIN_A1 = 14; // Arduino pin connected to DS18B20 sensor's DQ pin

OneWire oneWire(PIN_A1);                // setup a oneWire instance
DallasTemperature tempSensor(&oneWire); // pass oneWire to DallasTemperature library

float tempCelsius;    // temperature in Celsius

void setup()
{
  Serial.begin(9600); // initialize serial
  tempSensor.begin();    // initialize the sensor
}

void loop()
{
  tempSensor.requestTemperatures();             // send the command to get temperatures
  tempCelsius = tempSensor.getTempCByIndex(0);  // read temperature in Celsius
 
  Serial.print("Temperature: ");
  Serial.print(tempCelsius);    // print the temperature in Celsius
  Serial.println("°C");

  delay(500);
}

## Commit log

2023-01-17 Both esp32 and esp8266 supports now
2023-01-23 final project files
    [AquaMate.PcbDoc, AquaMate.SchDoc, AquaMate.step.SLDPRT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]
2023-02-16 servo library added
